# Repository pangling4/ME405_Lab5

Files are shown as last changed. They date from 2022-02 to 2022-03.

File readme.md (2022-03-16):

# ME 405 Winter 2022 Term Project: 3.5 Axis Machine
Created by Jonathan Cederquist, Tim Jain, and Philip Pang

## Introduction: Spider-Yoda, the 3-RRR Planar Parallel Robot
For this project our group designed, built, and tested a 3-RRR planar
parallel robot which we have nicknamed "Spider Yoda". This robot is
designed for us as a pen plotter for the average Joe who is interested
in a using a robotic companion to draw anything their heart desires.
Currently, it has only been used by the creators, but it could serve as
a device used to introduce high school or college students to robotics
and promote further interest and research in the field of robotics.

The overall functionality of the robot is quite simple. The moving
platform (which holds a Sharpie or other writing utensil) traces the
user's movements on the attached touchpad to produce a scaled drawing
of whatever path the user traces out. When the user places their finger
or stylus on the touchpad, the robot places the pen on the paper and
begins drawing whatever shape the user does. When the user lifts their
finger, the robot stops motion and the pen is retracted. In the future,
additional functionality may be added to allow the robot to draw on its
own from an uploaded image file. A schematic of a generic 3 RRR planar
parallel robot is shown below.

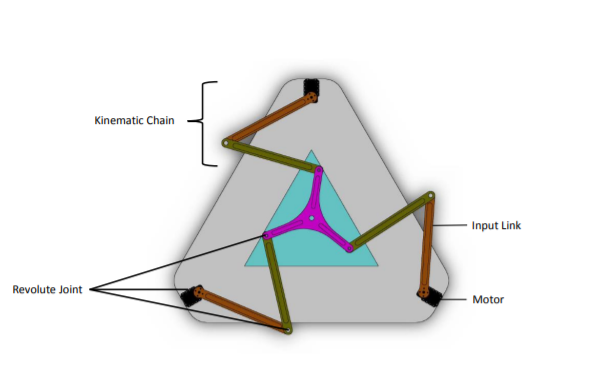
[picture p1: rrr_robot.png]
3-RRR Planar Parallel Robot!


*Figure 1: Schematic for a generic 3-RRR Planar Parallel Robot. [1]*

## Hardware Overview

### Bill of Materials
The following table shows the bill of materials used for our project. 
Minor components such as solder and wires are not included. It should
be noted that this table only lists the list price of each component,
tax and/or shippping are not included. This can be a significant
component of the project cost depending on the timeline and location
the products are sourced from.

| Qty. | Part | Source | Total Cost |
|:----:|:---|:---|:---: |
|  1 | Nucleo L476RG with Shoe | ME405 Tub | - |
|  6 | Aluminum Link | ME405 Scrap Bin | - |
|  1 | Aluminum Drawing Platform | ME405 Scrap Bin | - |
|  1 | 3D Printed Pen Holder | Friend's 3D printer | - |
|  1 | Black Fine Sharpie | Tim's Pencil Pouch | - |
|  ? | Other bolts/nuts | ME405 Hardware Stock  | - |
|  6 | M3-0.5 x 20mm SHCS | Home Depot | $1.98 |
|  1 | 2'x 2' Particle Board Base Plate | Home Depot | $4.23 |
|  15  | 1/4" Zinc Flat Washer | Home Depot | $2.40 |
|  10  | 1/4-20 Zinc Hex Nut | Home Depot | $1.28 |
|  3 | 6mm Set-Screw Shaft Collar 6056N14  | McMaster Carr | $5.31 |
|  6 | 5/16" Needle-Roller Thrust Bearing  | McMaster Carr | $19.14 |
|  6 | 5/16" Shoulder Screw | McMaster Carr | $8.52 |
|  3 | 12V Motor w/Encoder, 131 Gear Ratio | DFRobot | $87.00 |
|  1 | 12 VDC Open Frame Pull Solenoid | Chaocheng Technology  | $13.81 |
|  3 | MUZHI SPDT1NO Mtl Roller Lim Switch | Amazon | $1.83 |
|  3 | CHUANGRONG-US 1/3" SS Ball transfers| Amazon | $7.17 |

### Electronic Components
This project was built around the STM32 Nucleo L476RG microcontroller,
which was also equipped with the "Shoe of Brian" mounting board which
houses a USB on-the-go connector for easier file management. We also
used a DRI0039 quad motor driver shield from DFRobot, which implements
two TB6612FNG motor driver ICs, on top of the Nucleo to drive the three
gear motors and solenoid which lifted the pen. The motors used to drive
the motion of the links were FIT0185 DFRobot gear motors with encoders,
which have a 131:1 gear ratio and 2096 encoder counts per revolution on
the output shaft. The only other major electronic components were the
three roller limit switches, which were used in the calibration of the
robot before drawing began.

### Mechanical Components
Most of the structural mechanical components were found from the ME 405
scrap bin or purchased from Home Depot. The motors served as the stand
for the base platform, which was a 5/8"x2'x2' sheet of particle board
with holes drilled out for the motor shafts. The links and drawing
platform were aluminum scrap with holes reamed in them for close
fitting to the shoulder bolts. Each revolute joint connection included
two washers, a needle-roller thrust bearing to reduce friction, and a
shoulder bolt with a hex nut. The drawing platform itself had the 3D
printed pen holder and solenoid attached, along with ball transfers on
the bottom to support the platform and reduce friction as the robot
moved along the base plate. The rest of the components included wires,
attachement materials (hot glue, tape), and 3D printed limit switch
mounts which allowed the a-links to hold the limit switches for
calibration.

## Software Overview
This section summarizes the software organization for this project with
a task diagram and state transition diagram. The detailed documentation
is found on the doxygen mainpage, linked below:
https://pangling4.github.io/TermProject/

### Task Diagram
This section briefly explains the task organization for the cooperative
multitasking used in this project. The five tasks that were run by the
priority scheduler are shown below in the task diagram. Each joint task
consists of a RoboMotorDriver, a RoboEncoderDriver, and a ClosedLoop 
controller. The joint tasks receive the desired angle from the brain
and perform closed loop PI control using the motor and encoder to move
the link to the desired position. The angles are computed in the brain
from the inverse kinematic equations and the x and y coordinate which
are read from the touchpad.The readyFlag allows the motors and solenoid
to be shut off when the robot is ready to be shut down.

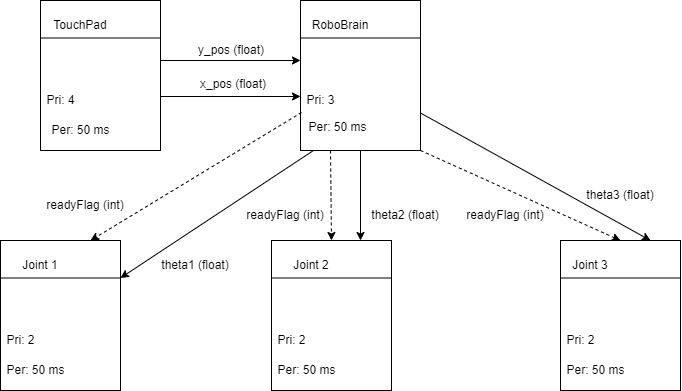
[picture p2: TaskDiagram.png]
3DOF Parallel Robot Task Diagram!


*Figure 2: Task Diagram for 3-RRR Planar Parallel Robot.*

### State Transition Diagram
The state transition diagram for our robot is shown below. The simple
layout is explained in more detail on the doxygen mainpage.

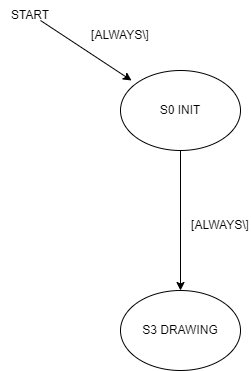
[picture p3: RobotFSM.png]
3DOF Parallel Robot State Transition Diagram!


*Figure 3: State Transition Diagram for 3-RRR Planar Parallel Robot.*

## Results
Overall, due to the limited timeline for the project, the system has
not been extensively tested. During the development of the controller
for the system, the motors underwent step response tests to determine
appropriate proportional and integral gains. However, these tests were
performed without any load on the motor shaft, as attaching the links
during a step response could damage the robot.

After final assembly, the robot was tested by having users draw on the
touchpad and observing the behavior. The robot's intended functionality
was evident in these tests, although it did not perform to our
satisfaction. One of the major problems we found was that the nature of
a parallel robot having interconnected and interdepedent links often
caused the robot to 'lock up' in a degenerate position where it could 
not move any of its links. When this happened, we had to restart the
robot and manually move the links back to a position where they could
move freely.

Other issues we became aware of during testing were the backlash in the
a-links and the method of control for the inverse kinematics. Both of 
these issues contributed to 'sloppy' behavior for the drawing platform,
since a motion on the touchpad would either not be large enough to 
cause a motion on the platform (due to small angle changes and large 
backlash), or the motion would be overwritten by the next motion since
the links were not able to respond fast enough. Thus, the actual motion
of the drawing platform did not match the motion of the user's hand on
the touchpad.

## Project Learning Outcomes
Overall, this project was more difficult and time-consuming than we
expected, mainly because of the mechanical complexities in our design
and difficulties we encountered during manufacturing and assembly. The
following sections describe some of the major difficulties we faced and
future recommendations for others who build a similar robot.

### Difficulties Encountered
One major problem we encountered while assembling our robot was getting
the a-links to attach securely to the motor shafts. Our original design 
used steel shaft collars with set screws that would be epoxied to the
a-links and then securely tightened onto the d-flat of the motor shaft.
However, the shaft collars would consistently fall off of the a-links
during testing and loading, likely because the surfaces were not well
prepared for epoxy and possibly because the metals being bonded were
not the same (steel vs aluminum). In the final robot, we used d-shaped
holes waterjet into the links directly, but due to the small difference
in diameter between the motor shaft OD and d flat, these ended up
having large amounts of backlash.

Another issue we encountered was in calibration. After creating the 3D
printed mounts for the limit switches and ramps used to locate a known
location for each link, we realized that having the mounts on the links
interfered with the robot motion in some configurations. This could 
have been mitigated by shifting the limit switches closer to the motors
on the link; however, the ramp had already been glued down on the base.
One solution to this problem would be to make longer ramps to allow the
limit switch to slide along the link to any necessary location. An even
better solution would be to embedd the limit switches in the base and
mount the ramps to the bottom of the link, thus reducing the wiring
complexity and allowing the links to move freely without interference.
However, due to the time constraint on the project, we were not able to
implement these improvements.

### Future Recommendations
Overall, the most important recommendation we can offer anyone desiring
to build a similar project is to spend adequate time on the mechanical
design. Creating detailed models, testing the connection methods and
layout, and iterating on failed designs are all important steps in the
design process that should not be skipped. Even the best-written
software is useless if the motor shaft is not securely attached to the
robot link.

Part of the challenge on this project for our team was the limited time
given to complete it. Do not underestimate the time necessary for 
manufacturing your robot. In addition, it is very helpful to buy or
make spare parts for your robot, since you never know when your epoxy connection will 
shear off and you will need to take 45 minutes to use a tiny 1/2" thick hacksaw
blade to gnaw away a stripped shoulder bolt at 1 am the night before it is due.
Other complications could be that a screw head
will strip, or glue will come loose, or other issue will occur that requires a
replacement. Software can be updated and improved (relatively) easily,
requiring only time to debug and test. On the other hand, updating or
improving mechanical hardware can be significantly more challenging,
especially if tools or materials are not readily available.

## CAD
The mechanical design for this project was performed in SolidWorks. All
of the models created for the project can be found under the src folder
in the CAD Rev4 folder, which has been updated to reflect the actual
dimensions and layout of the robot as-built. The wiring and attachment
components (such as tape and hot glue) are not shown.

Link: https://github.com/pangling4/TermProject/tree/main/src/CAD%20Rev4

[1] G. Johnston, R. Yasin, L. Wang, N. Sarli, and N. Simaan, “Parallel 
3RRR Robot Classroom Guide,” 07-Jul-2016. [Online]. Available: 
http://nri-csa.vuse.vanderbilt.edu/joomla/images/Harpeth_Hall_Winterim/Parallel_3RRR_Robot_Classroom_Guide.pdf. [Accessed: 25-Feb-2022].

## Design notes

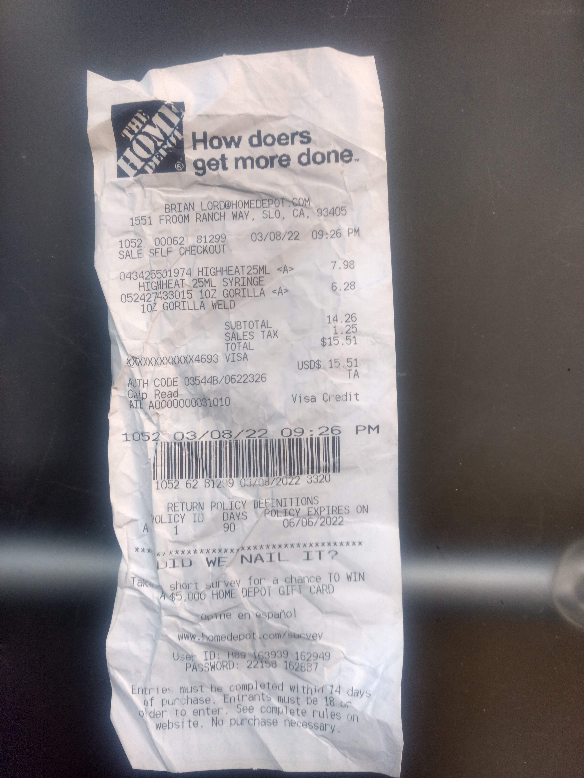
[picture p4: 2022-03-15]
Epoxy1.jpg

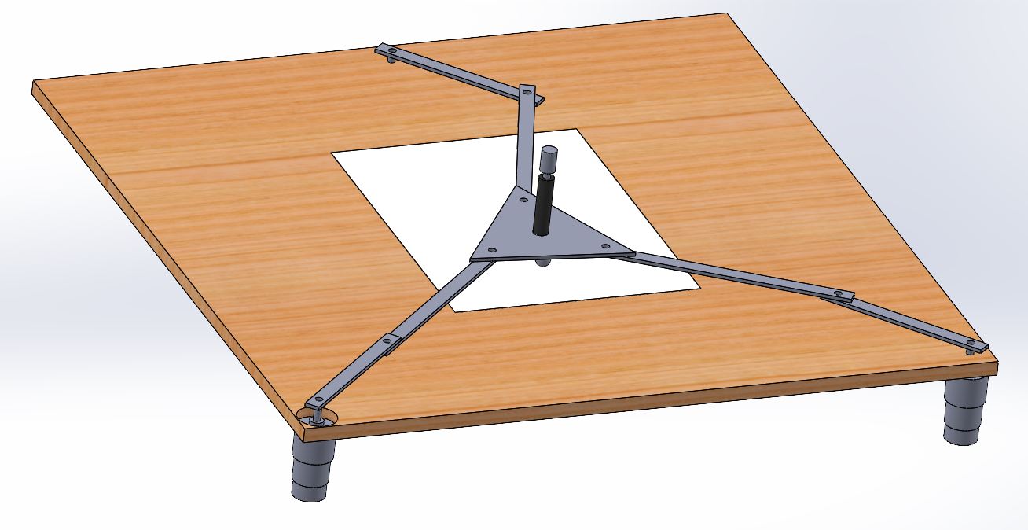
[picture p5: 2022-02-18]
3R_iso_2.JPG

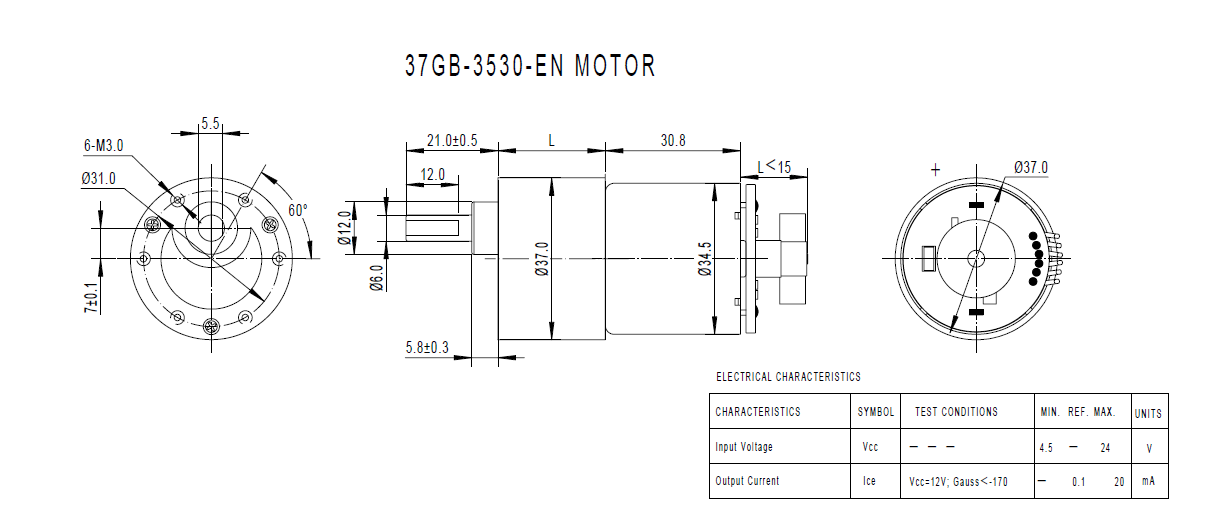
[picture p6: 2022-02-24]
motor_dims.png

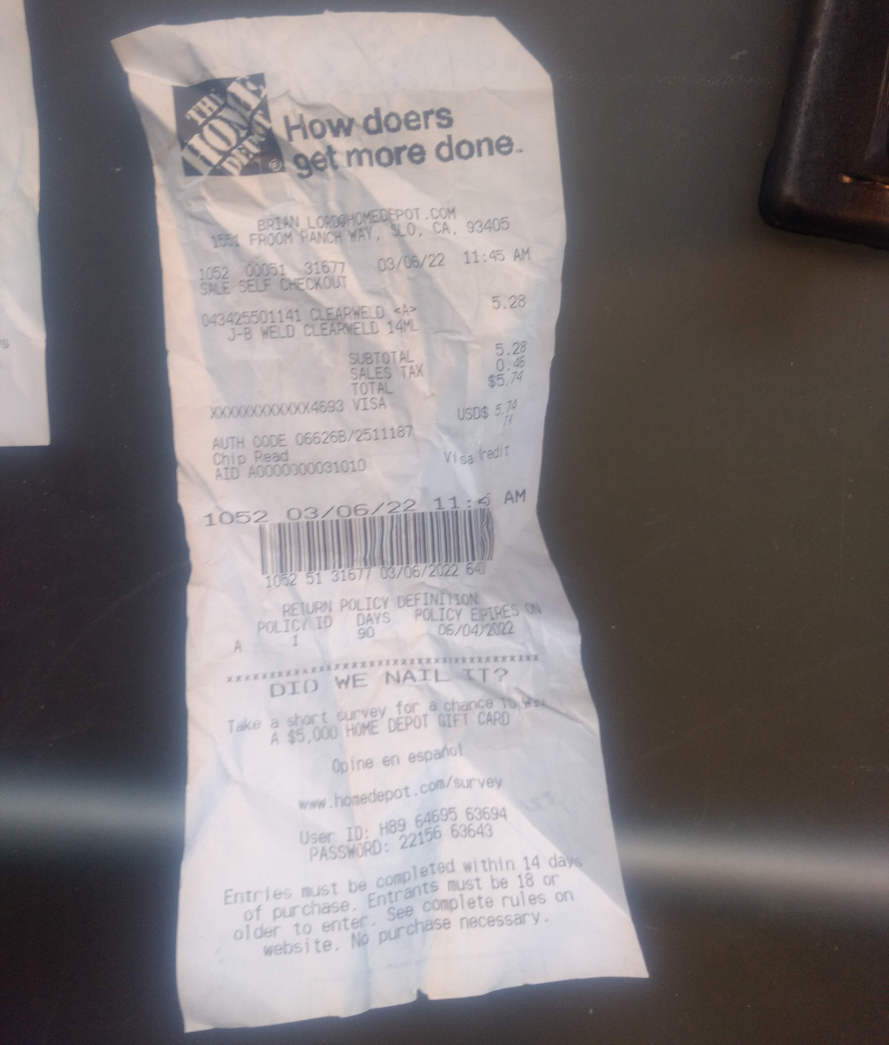
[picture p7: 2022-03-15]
JBWeld.jpg

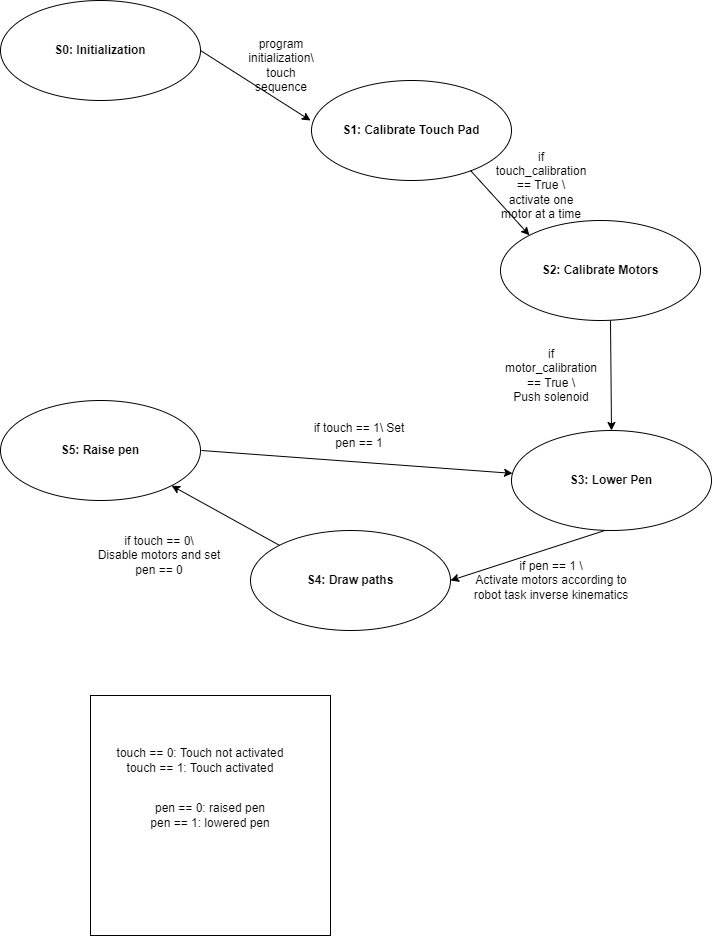
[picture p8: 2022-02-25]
3R_FSM_Touch.drawio.png

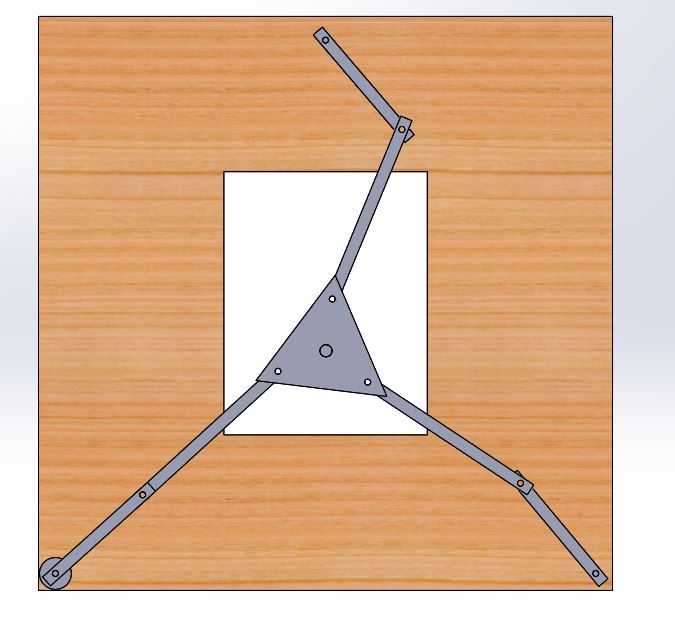
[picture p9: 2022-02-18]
3R_top_cad.JPG

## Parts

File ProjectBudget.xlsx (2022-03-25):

Item | Quantity | Per Item | Price | Buyer | Vendor
JB ClearWeld | 1 | $5.74 | $5.74 | Tim | Home Depot
HighHeat Epoxy | 1 | $7.98 | $7.98 | Tim | Home Depot
Thrust Bearings | 6 | $3.19 | $19.14 | Tim | McMaster-Carr
Shoulder Screws | 6 | $1.42 | $8.52 | Tim | McMaster-Carr
Shaft Collar | 3 | $1.77 | $5.31 | Tim | McMaster-Carr
Unthreaded Spacers | 3 | $1.77 | $5.31 | Tim | McMaster-Carr
McMaster Shipping and Tax | 1 | $11.88 | $11.88 | Tim | McMaster-Carr
 |  |  | $0.00
 |  |  | $0.00
 |  |  | $0.00
 |  |  | $0.00
 |  |  | $0.00
 |  |  | $0.00
 |  |  | $0.00
 |  |  | $0.00
 |  |  | $0.00
 |  |  | $0.00
 |  |  | $0.00
 |  |  | $0.00

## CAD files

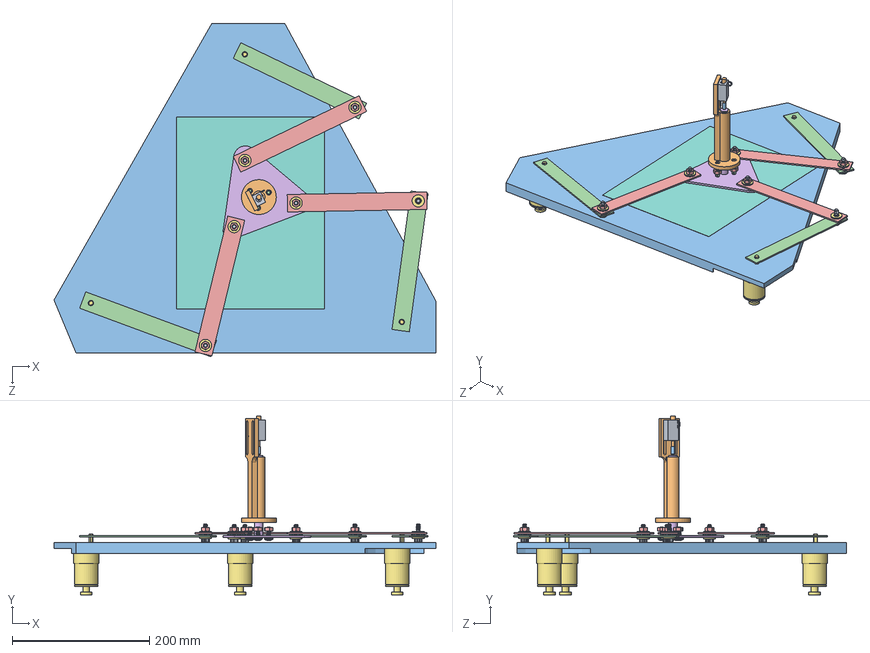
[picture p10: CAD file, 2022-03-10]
src/CAD Rev4/10_Full_3R_Assembly_rev4.SLDASM
555.8 x 260.0 x 485.0 mm
01_Base_Plate_rev4
02_A_Link x 3
03_B_Link x 3
05_Pen
07_Motor_rev2 x 3
5909K24_Needle-Roller Thrust Bearing x 6
91259A576_Alloy Steel Shoulder Screw x 6
PenHolder
Solenoid_Mount
Solenoid_Shaft
Solenoid_Cap
90604A539_Pan Head Combination Phillips Slotted Screws x 3
95462A029_Medium-Strength Steel Hex Nut x 9
Platform_Alt
90850A150_Grade 9 Steel Washer x 12
06_Paper

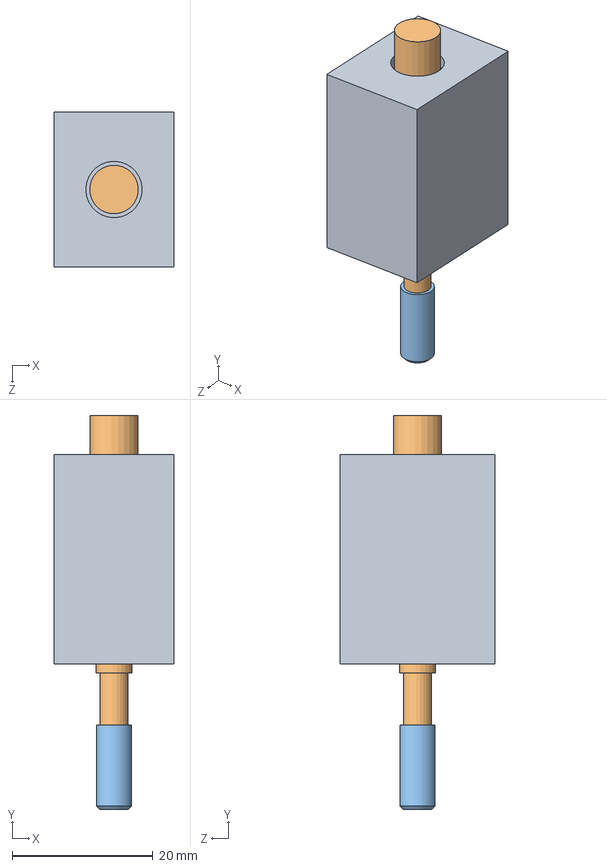
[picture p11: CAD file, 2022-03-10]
src/CAD Rev4/SolenoidAssembly.SLDASM
17.0 x 55.9 x 22.0 mm
Solenoid_Mount
Solenoid_Shaft
Solenoid_Cap

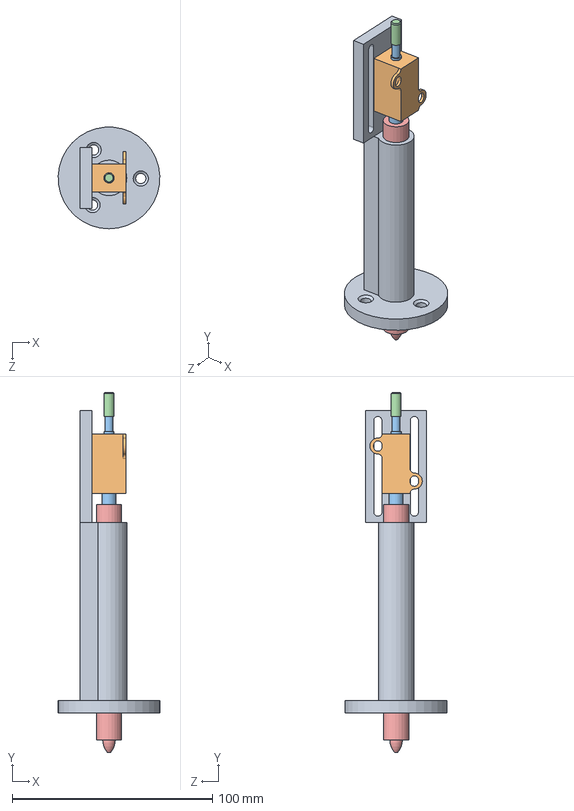
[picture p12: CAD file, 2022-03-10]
src/CAD Rev4/PenHoldingAssembly.SLDASM
50.7 x 179.7 x 50.7 mm
PenHolder
Solenoid_Mount
Solenoid_Shaft
Solenoid_Cap
05_Pen

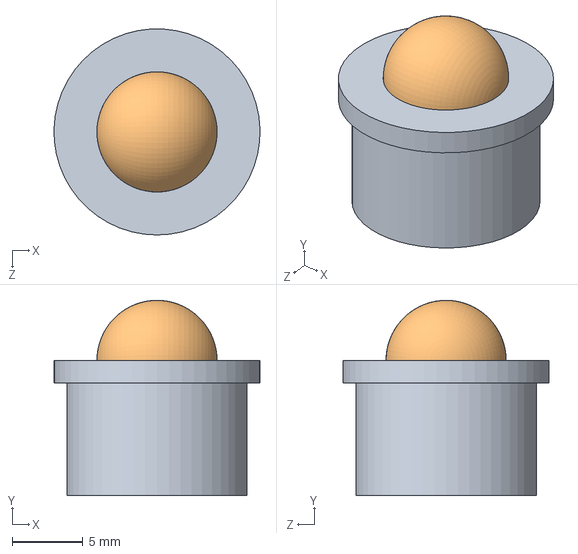
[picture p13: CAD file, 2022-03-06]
src/CAD Rev4/10_Ball_Transfer.SLDASM
14.5 x 13.8 x 14.5 mm
09_Ball_Holder
08_Ball

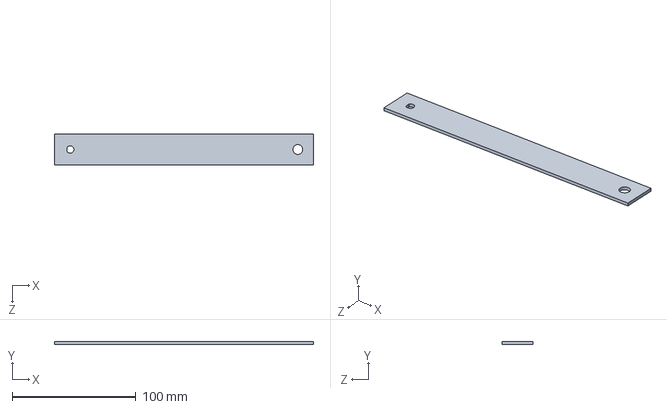
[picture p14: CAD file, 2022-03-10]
src/CAD Rev4/Master_Link.SLDPRT
209.5 x 2.29 x 25.4 mm

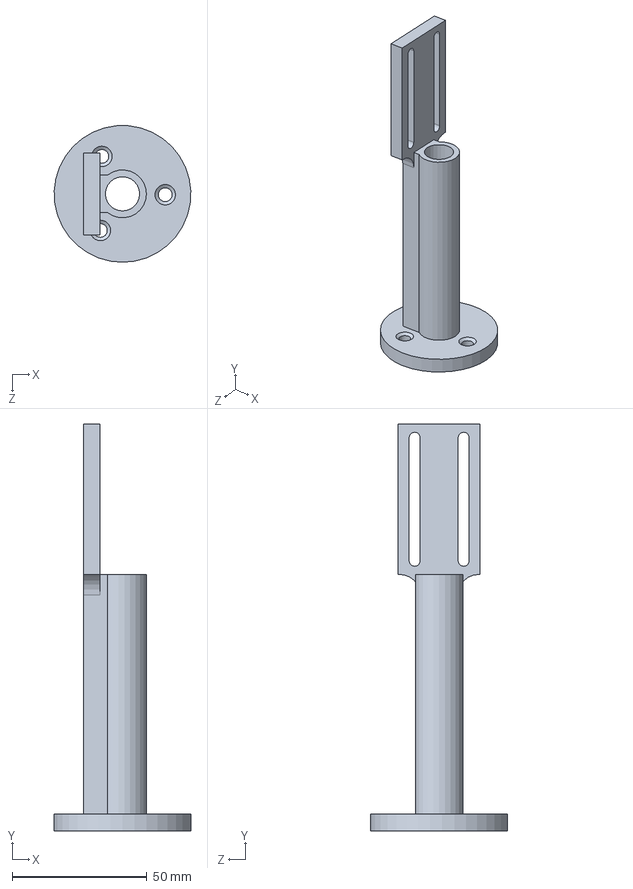
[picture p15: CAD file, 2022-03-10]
src/CAD Rev4/PenHolder.SLDPRT
50.7 x 151.1 x 50.7 mm

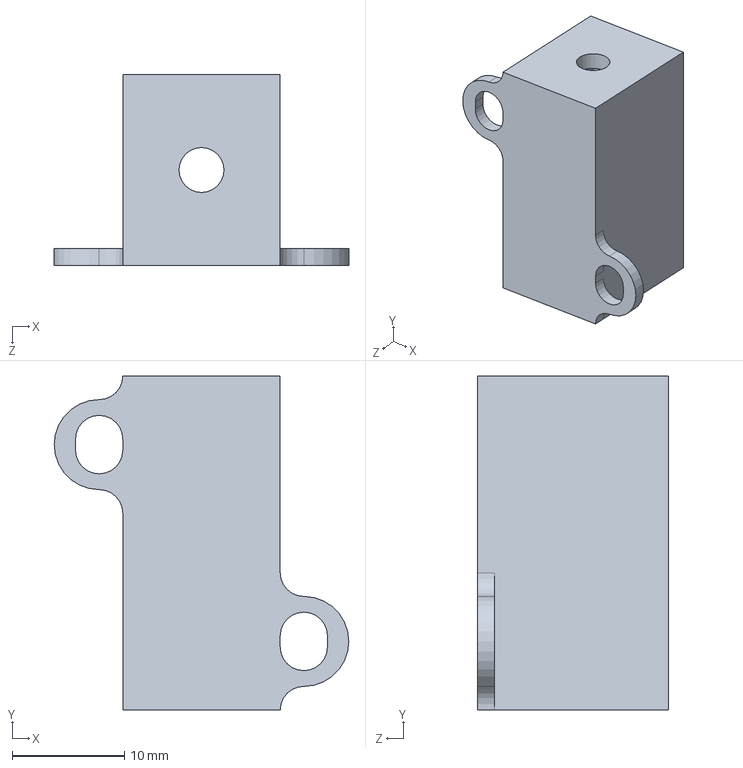
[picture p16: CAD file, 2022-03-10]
src/CAD Rev4/Solenoid_Mount.SLDPRT
26.2 x 29.7 x 17.0 mm

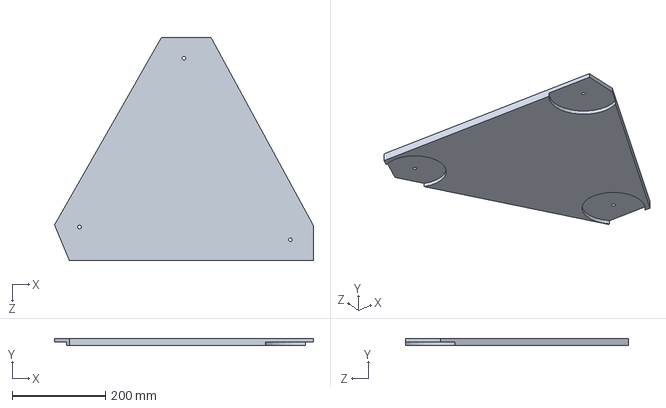
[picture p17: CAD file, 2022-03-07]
src/CAD Rev4/01_Base_Plate_rev4.SLDPRT
555.8 x 15.9 x 479.4 mm

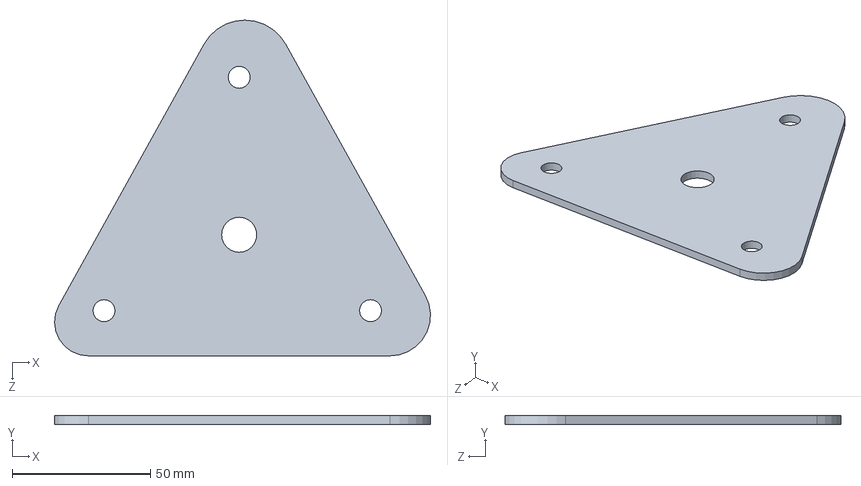
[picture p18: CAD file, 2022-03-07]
src/CAD Rev4/Platform_Alt.SLDPRT
136.0 x 3.17 x 121.5 mm

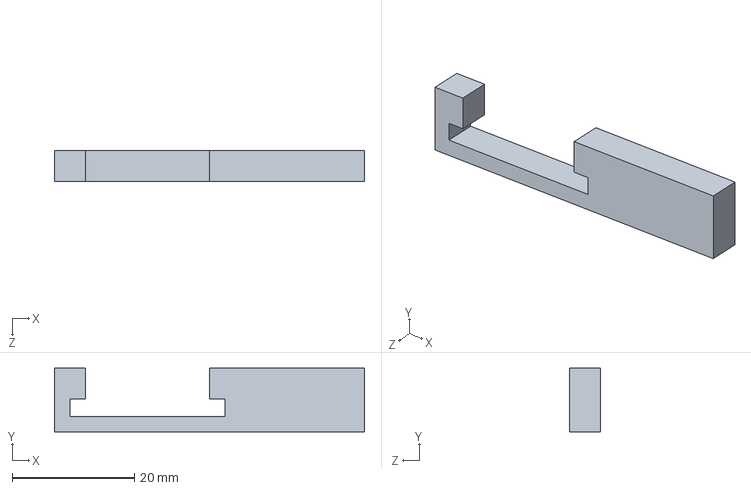
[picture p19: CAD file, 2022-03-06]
src/CAD Rev4/12_Limit_Mount.SLDPRT
50.8 x 10.4 x 5.08 mm

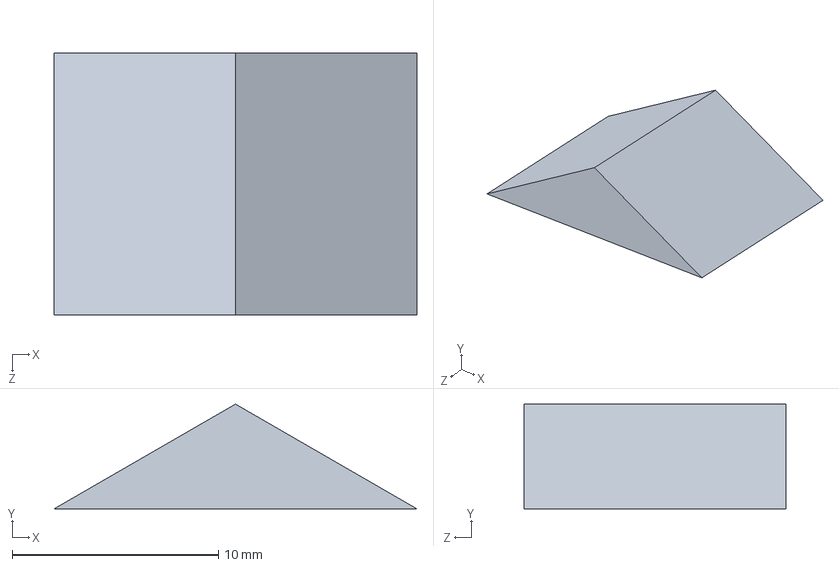
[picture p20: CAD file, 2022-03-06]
src/CAD Rev4/13_Limit_Ramp.SLDPRT
17.6 x 5.08 x 12.7 mm

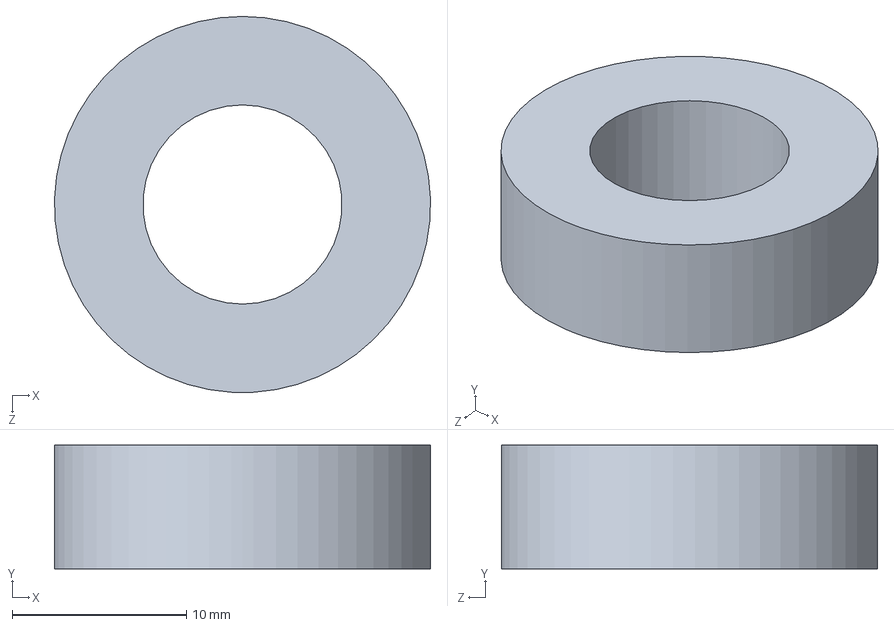
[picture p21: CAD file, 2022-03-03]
src/CAD Rev4/09_Ball_Holder.SLDPRT
21.6 x 7.11 x 21.6 mm

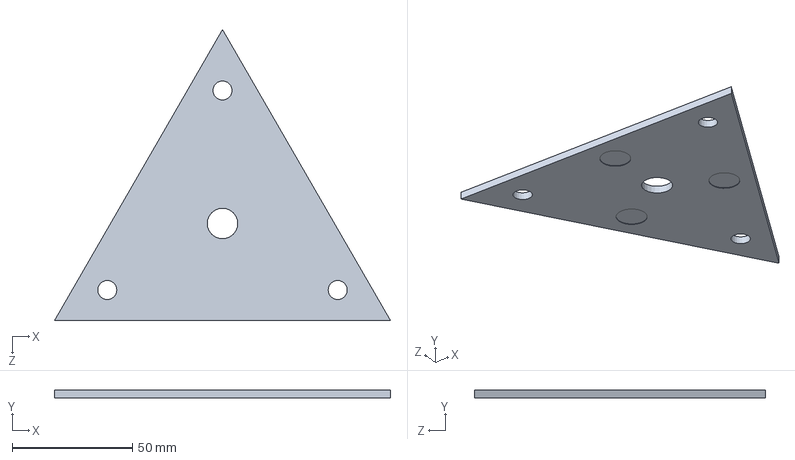
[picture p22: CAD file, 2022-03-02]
src/CAD Rev4/04_Platform.SLDPRT
140.0 x 3.17 x 121.2 mm

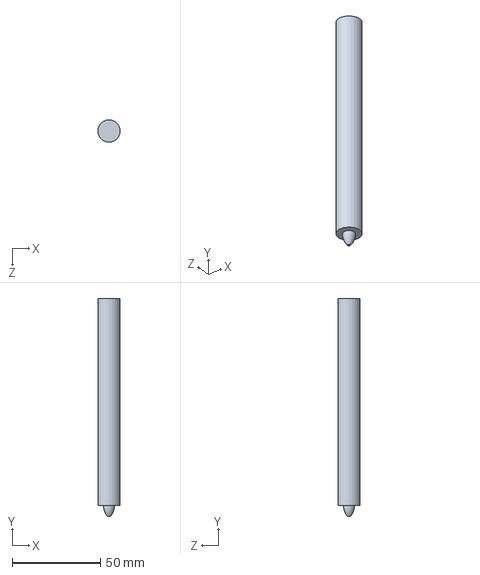
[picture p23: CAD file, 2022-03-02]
src/CAD Rev4/05_Pen.SLDPRT
12.7 x 123.8 x 12.7 mm

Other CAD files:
src/CAD Rev4/Solenoid_Cap.SLDPRT
src/CAD Rev4/Solenoid_Shaft.SLDPRT
src/CAD Rev4/07_Motor_rev2.SLDPRT
src/CAD Rev4/grainger-2alx5.sldprt
src/CAD Rev2/01_Base_Plate.SLDPRT
src/CAD Rev2/01_Base_Plate_rev2.SLDPRT
src/CAD Rev2/01_Base_Plate_rev3.SLDPRT
src/CAD Rev2/02_A_Link.SLDPRT
src/CAD Rev2/03_B_Link.SLDPRT
src/CAD Rev2/06_Paper.SLDPRT
src/CAD Rev2/10_Full_3R_Assembly_rev2.SLDASM
src/CAD Rev2/10_Full_3R_Assembly_rev3.SLDASM
src/CAD Rev2/11_Solenoid_rev2.SLDPRT
src/CAD Rev2/1_ALink.SLDPRT
src/CAD Rev2/Motor_Mount.SLDPRT
src/CAD Rev2/Spacer_Platform.SLDPRT
src/CAD Rev4/02_A_Link.SLDPRT
src/CAD Rev4/03_B_Link.SLDPRT
src/CAD Rev4/08_Ball.SLDPRT
src/CAD Rev4/08_Roller.SLDPRT
src/CAD Rev4/5909K24_Needle-Roller Thrust Bearing.SLDPRT
src/CAD Rev4/6056N14_Carbon Steel Set Screw Collar.SLDPRT
src/CAD Rev4/90604A539_Pan Head Combination Phillips Slotted Screws.SLDPRT
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

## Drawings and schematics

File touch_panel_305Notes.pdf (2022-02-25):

# Lecture 21 - 4-Wire Resistive Touch Panels

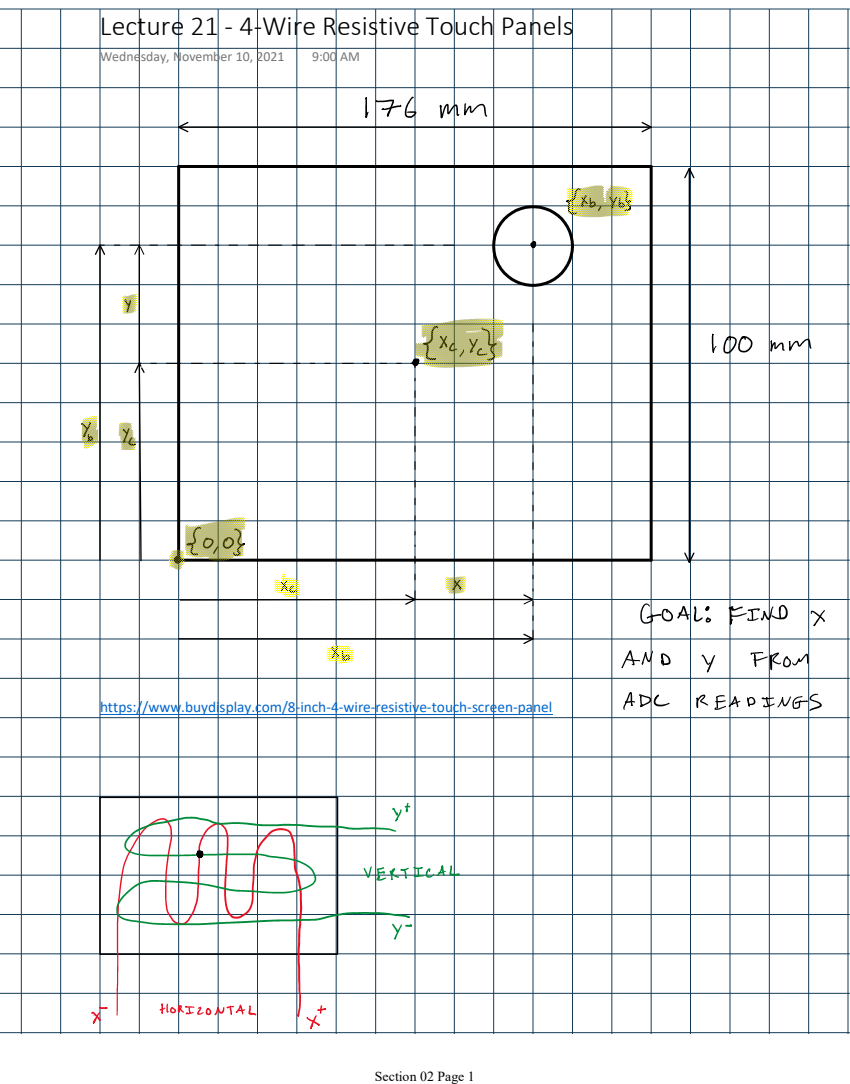
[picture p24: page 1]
Wednesday, November 10, 2021; Section 02 Page 1

https://www.buydisplay.com/8-inch-4-wire-resistive-touch-screen-panel

# Equivalent Circuit

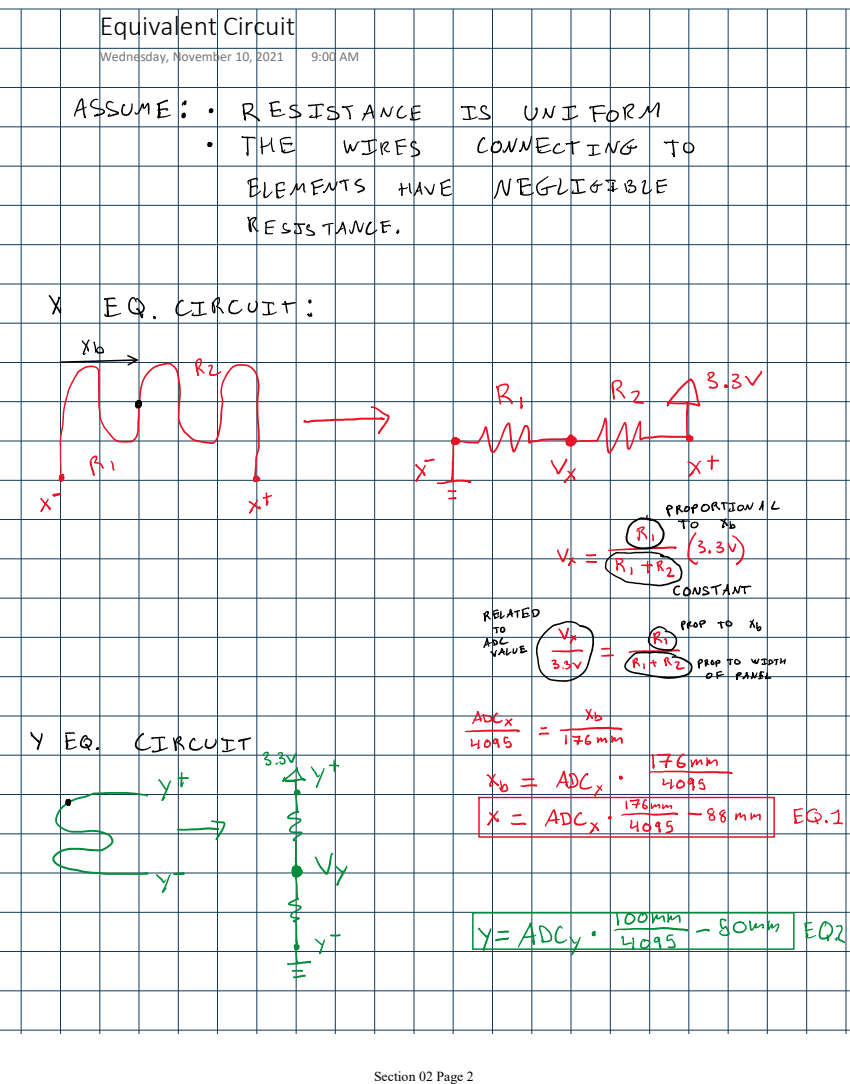
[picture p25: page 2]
Section 02 Page 2

# X Scan

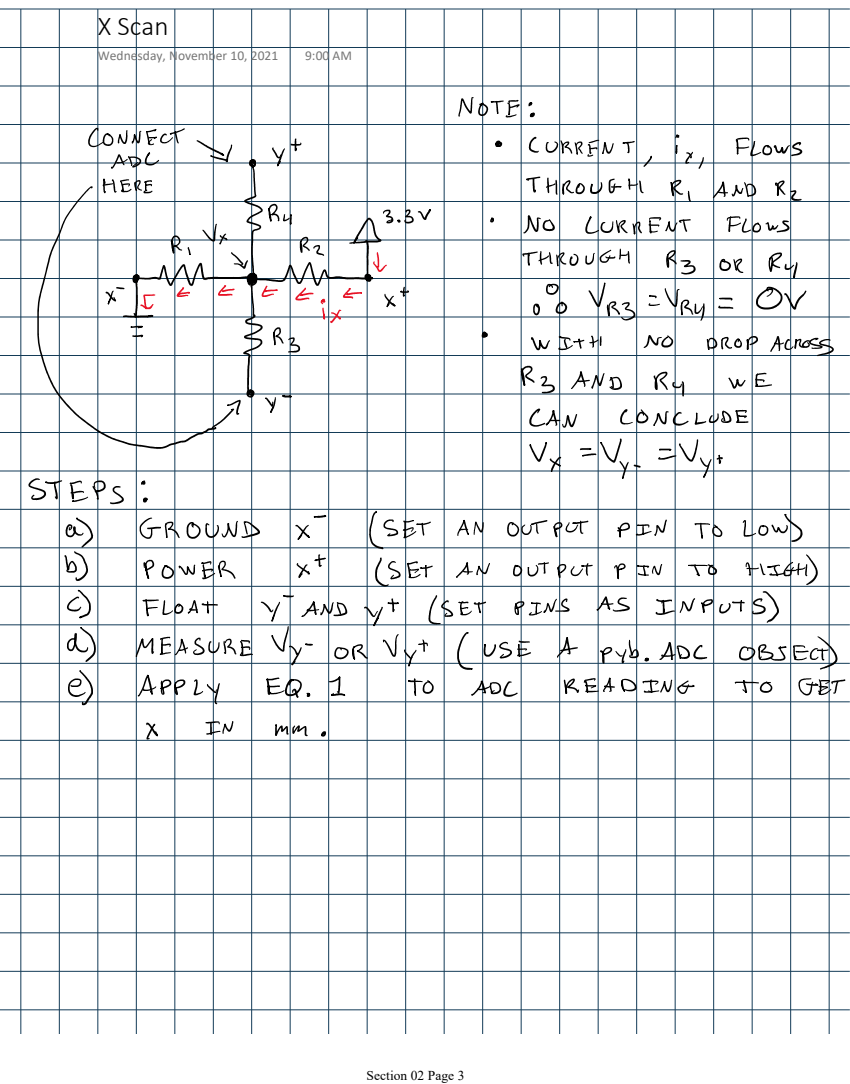
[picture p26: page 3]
Section 02 Page 3

# Y Scan

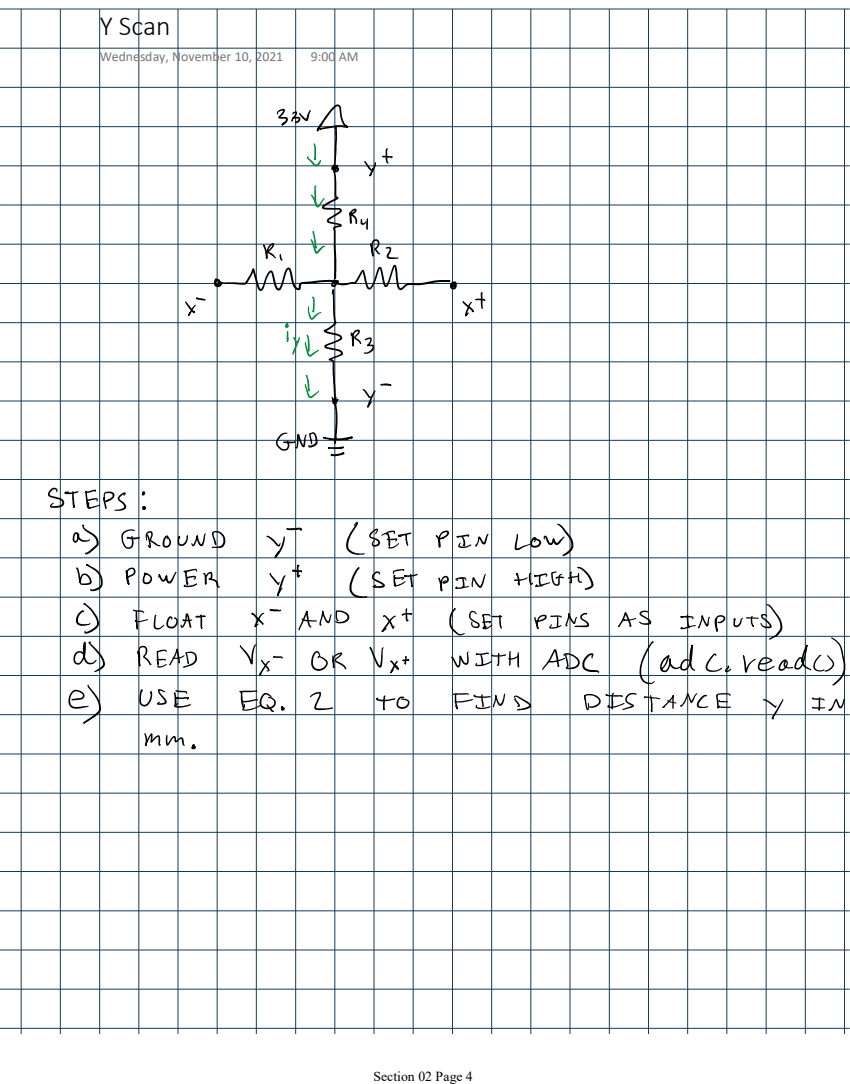
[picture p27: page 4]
Section 02 Page 4

# Z Scan

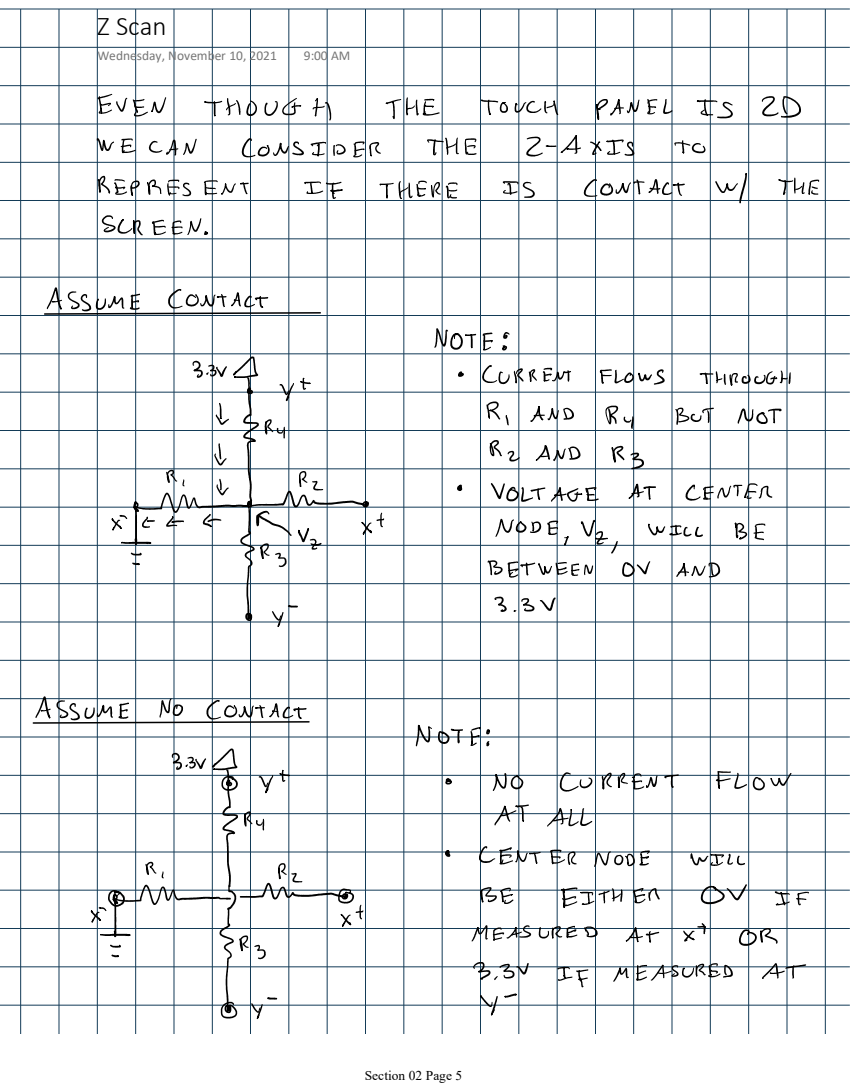
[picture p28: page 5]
Section 02 Page 5

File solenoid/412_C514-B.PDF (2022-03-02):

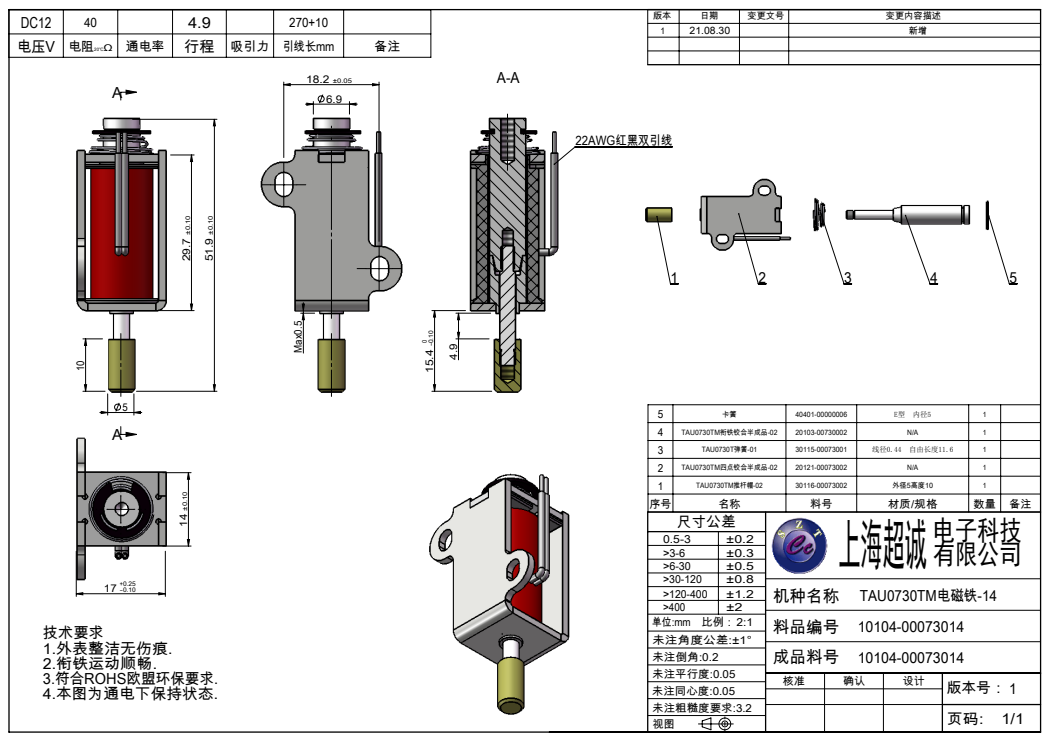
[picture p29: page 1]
2:1 技术要求

5 | 卡簧 | 40401-00000006 | E型 内径5 | 1
4 | TAU0730TM衔铁铰合半成品-02 | 20103-00730002 | N/A | 1
3 | TAU0730T弹簧-01 | 30115-00073001 | 线径0.44 自由长度11.6 | 1
2 | TAU0730TM四点铰合半成品-02 | 20121-00073002 | N/A | 1
1 | TAU0730TM推杆帽-02 | 30116-00073002 | 外径5高度10 | 1
序号 | 名称 | 料号 | 材质/规格 | 数量 | 备注
尺寸公差 | 上海超诚 电子科技 有限公司
0.5-3 | ±0.2
>3-6 | ±0.3
>6-30 | ±0.5
>30-120 | ±0.8

核准 | 确认 | 设计 版本号： 1 1/1 页码:

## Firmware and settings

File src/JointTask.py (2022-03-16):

'''!
@file       jointTask.py
@brief      Implements motor, encoder, and controller to control joints
@details    Creates a motor driver, encoder, and closed loop controller corresponding to
            a joint on the 3RRR planar parallel robot. The run function is used by
            the cotask scheduler to control the motion of each joint
@author     Jonathan Cederquist
@author     Tim Jain
@author     Philip Pang
@date       Last Modified 3/5/22
'''

import pyb
import utime
import RoboMotorDriver
import RoboEncoderDriver
import ClosedLoop

class JointTask:
    '''! 
    This class implements a motor, encoder, and control task to control robot joints. 
    '''
    
    def __init__ (self, ready, motor_const, encoder_const, kp, ki, setpoint, queue_theta):
        '''! 
        @brief                  Creates a JointTask object
        @details                Creates RoboMotorDriver, RoboEncoderDriver, and ClosedLoop
                                controller objects corresponding to the given constants to
                                control the motion of a joint on the 3 RRR planar parallel
                                robot.
        @param ready            A task_share.Share variable that is used as a flag to turn
                                off the joint motor when the robot shuts down
        @param motor_const      An integer denoting the motor associated with the joint.
                                Motor 1 corresponds to M1, pins PB5 and PB3
                                Motor 2 corresponds to M2, pins PA6 and PA7
                                Motor 3 corresponds to M3, pins PA9 and PB4
        @param encoder_const    An integer denoting the encoder associated with the motor.
                                Encoder 1 corresponds to pins PB6 and PB7 with timer 4
                                Encoder 2 corresponds to pins PC6 and PC7 with timer 8
                                Encoder 3 corresponds to pins PA0 and PA1 with timer 5
        @param kp               The proportional gain constant used for the closed loop controller
                                The constant should be given in units of [% duty cycle/degree]
        @param ki               The integral gain constatn used for the closed loop controller
                                The constant should be given in units of [% duty cycle * sec/degree]
        @param setpoint         The setpoint in degrees for the closed loop controller
        @param queue_theta      The task_share.Queue corresponding to this joint's theta value
        '''
        
        self.motor_const = motor_const
        
        self.ready = ready
        
        # Check motor number and create corresponding RoboMotorDriver
        if motor_const==1:
            pinB5 = pyb.Pin(pyb.Pin.board.PB5, pyb.Pin.OUT_PP)
            pinB3 = pyb.Pin(pyb.Pin.board.PB3, pyb.Pin.OUT_PP)
    
            self.motor = RoboMotorDriver.RoboMotorDriver(pinB5, pinB3, 2, 2)
            
        elif motor_const==2:
            pinA6 = pyb.Pin(pyb.Pin.board.PA6, pyb.Pin.OUT_PP)
            pinA7 = pyb.Pin(pyb.Pin.board.PA7, pyb.Pin.OUT_PP)
    
            self.motor = RoboMotorDriver.RoboMotorDriver(pinA6, pinA7, 3, 2)
            
        elif motor_const==3:
            pinA9 = pyb.Pin(pyb.Pin.board.PA9, pyb.Pin.OUT_PP)
            pinB4 = pyb.Pin(pyb.Pin.board.PB4, pyb.Pin.OUT_PP)
    
            self.motor = RoboMotorDriver.RoboMotorDriver(pinA9, pinB4, 3, 1)
        
        self.motor.set_duty_cycle(0)
        
        # Check encoder number and create corresponding RoboEncoderDriver
        if encoder_const==1:
            self.encoder = RoboEncoderDriver.RoboEncoderDriver(pyb.Pin(pyb.Pin.board.PB6), pyb.Pin(pyb.Pin.board.PB7), 4)
            
        elif encoder_const==2:
            self.encoder = RoboEncoderDriver.RoboEncoderDriver(pyb.Pin(pyb.Pin.board.PC6), pyb.Pin(pyb.Pin.board.PC7), 8)
            
        elif encoder_const==3:
            self.encoder = RoboEncoderDriver.RoboEncoderDriver(pyb.Pin(pyb.Pin.board.PA0), pyb.Pin(pyb.Pin.board.PA1), 5)
            
        # Create closed loop controller
        self.controller = ClosedLoop.ClosedLoop(kp, ki, setpoint)
        
        # Create variable to access queue of position values
        self.theta_queue = queue_theta
        
        # Create joint angle value
        self.theta = 0
        
        # Run calibration on creation of each joint
        self.calibrate()
        
        
    def run(self):
        '''!
        @brief      Generator which continuously updates the joint
        @details    Pulls the desired position from a shared queue, and updates
                    the joint motor, encoder, and controller accordingly
        '''
        
        while True:
            #Update angle from shared kinematics
            
            if self.ready.get() == 0:
                self.motor.set_duty_cycle(0)
                print("Motor Off")
                
            else:
                if self.theta_queue.any():
                    newTheta = self.theta_queue.get()
                else:
                    newTheta = self.theta
                if self.theta != newTheta:
                    self.theta = newTheta
                    self.controller.change_setpoint(self.theta)
                
                # Update encoder and change control signal
                self.encoder.update()
                self.motor.set_duty_cycle(self.controller.update(self.encoder.read()))
            yield(0)

    def calibrate(self):
        '''!
        @brief      Calibrates the joint encoder to the correct position
        @details    Waits for the user to manually move the link past the limit
                    switch ramp and sets the encoder value to the correct angle
                    after the link has moved back and forth across the limit
                    switch ramp.
        '''
        
        if self.motor_const == 1:
            limit = pyb.Pin(pyb.Pin.cpu.C4, pyb.Pin.PULL_DOWN)
            theta1 = 4
            theta2 = 6
        elif self.motor_const == 2:
            limit = pyb.Pin(pyb.Pin.cpu.C1, pyb.Pin.PULL_DOWN)
            theta1 = 122
            theta2 = 124
        elif self.motor_const == 3:
            limit = pyb.Pin(pyb.Pin.cpu.A5, pyb.Pin.PULL_DOWN)
            theta1 = 242
            theta2 = 243
        
        print("Calibrating motor " + str(self.motor_const))
        
        count = 0
        press = 0
        clicks = [0, 0]
        
        while True:
            self.encoder.update()
            if press == 1 and limit.value() == 0:
                press = 0
            if press == 0 and limit.value() == 1:
                clicks[count] = self.encoder.read()
                count += 1
                press = 1
                print("Limit found")
                
                if count == 2:
                    if(clicks[0] > clicks[1]):
                        self.encoder.setTheta(theta1)
                    elif (clicks[1] > clicks[0]):
                        self.encoder.setTheta(theta2)
                    else:
                        self.encoder.setTheta((theta1+theta2)/2)
                    print("calibration complete")
                    break
                
        
if __name__ == "__main__":
    pass
    

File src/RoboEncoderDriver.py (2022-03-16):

'''!
@file       roboEncoderDriver.py
@brief      Used to read from encoders attached to motors (No. GB37Y3530-12V-83R)
@details    Utilizes alternate functions from timer channels on pyb board to 
            read from attached encoders
@author     Jonathan Cederquist
@author     Tim Jain
@author     Philip Pang
@date       Last Modified 3/3/22
'''

import pyb
import utime
import RoboMotorDriver

class RoboEncoderDriver:
    '''! 
    This class implements an encoder driver for an ME 405 Robot. 
    '''
    gearRatio = 131
    CPR = 16
    
    def __init__ (self, in1pin, in2pin, timer):
        '''! 
        @brief          Creates an RoboEncoderDriver object
        @details        Creates a RoboEncoderDriver by initializing timers and channels with 
                        given pins and timer number
        @param in1pin   A pyb.Pin object corresponding to the encoder channel A 
        @param in2pin   A pyb.Pin object corresponding to the encoder channel B
        @param timer    The timer number corresponding to the encoder pins
        '''
        
        # Create timer and timer channels in encoder mode
        self.timer = pyb.Timer(timer, prescaler = 0, period = 65535)
        self.ch1 = self.timer.channel(1, pyb.Timer.ENC_A, pin = in1pin)
        self.ch2 = self.timer.channel(2, pyb.Timer.ENC_B, pin = in2pin)
        
        # Stores current encoder position in radians
        self.current_position = 0
        self.delta = 0
        

    def update(self):
        '''!
        @brief      Updates the position of the encoder 
        @details    Updates the position of the encoder using saved last value
                    Checks for a 'valid' delta and adjusts if needed, then adds
                    delta to previous position 
        '''

        prev_position = self.current_position % 65535
        self.delta = self.timer.counter() - prev_position
        
        # Validate and adjust delta
        if self.delta < -65535/2:
            self.delta += 65535
        elif self.delta > 65535/2:
            self.delta -= 65535
        
        # Update position
        self.current_position += self.delta
        return self.current_position
    
    def read (self):
        '''!
        @brief      Returns current position of encoder
        @details    Converts the current encoder position reading (in ticks)
                    to degrees using the encoder CPR and gear ratio
        '''        
        return self.current_position * 180 / (self.gearRatio*self.CPR)
    

    def zero(self):
        '''!
        @brief      Zeros the encoder position
        '''
        
        self.current_position = 0
        self.delta = 0
        self.timer.counter(0)
    
    def setTheta(self, theta):
        '''!
        @brief       Sets the theta position of the encoder to the given value
        @param theta The angle (in degrees) to set the encoder's position to
        '''
        self.current_position = theta*self.gearRatio*self.CPR/180
        self.delta = 0
        self.timer.counter(0)
        
        
if __name__ == "__main__":
    
    encoder1 = RoboEncoderDriver(pyb.Pin(pyb.Pin.board.PB6), pyb.Pin(pyb.Pin.board.PB7), 4)
    encoder2 = RoboEncoderDriver(pyb.Pin(pyb.Pin.board.PC6), pyb.Pin(pyb.Pin.board.PC7), 8)
    encoder3 = RoboEncoderDriver(pyb.Pin(pyb.Pin.board.PA0), pyb.Pin(pyb.Pin.board.PA1), 5)
    
    
    # Instantiates three motor driver objects with appropriate pins and timer number
    pinB5 = pyb.Pin(pyb.Pin.board.PB5, pyb.Pin.OUT_PP)
    pinB3 = pyb.Pin(pyb.Pin.board.PB3, pyb.Pin.OUT_PP)
    
    motor1 = RoboMotorDriver.RoboMotorDriver(pinB5, pinB3, 2, 2)
    
    # Motor 2
    pinA6 = pyb.Pin(pyb.Pin.board.PA6, pyb.Pin.OUT_PP)
    pinA7 = pyb.Pin(pyb.Pin.board.PA7, pyb.Pin.OUT_PP)
    
    motor2 = RoboMotorDriver.RoboMotorDriver(pinA6, pinA7, 3, 2)
    
    # Motor 3
    pinA9 = pyb.Pin(pyb.Pin.board.PA9, pyb.Pin.OUT_PP)
    pinB4 = pyb.Pin(pyb.Pin.board.PB4, pyb.Pin.OUT_PP)
    
    motor3 = RoboMotorDriver.RoboMotorDriver(pinA9, pinB4, 3, 1)
    
    try:
        # Start motor 1, 2, 3
        motor1.set_duty_cycle(20)
        motor2.set_duty_cycle(20)
        motor3.set_duty_cycle(20)
        
        time = utime.ticks_ms()
        
        #while utime.ticks_ms() < (time + 10000):
        while True:
            encoder1.update()
            encoder2.update()
            encoder3.update()
            
            if (utime.ticks_ms() > (time + 50)):
                print("\ntimer counter1:", encoder1.timer.counter())
                print("\nencoder driver1", encoder1.read())
                
                print("\ntimer counter2:", encoder2.timer.counter())
                print("\nencoder driver2", encoder2.read())
                
                print("\ntimer counter3:", encoder3.timer.counter())
                print("\nencoder driver3", encoder3.read())
                
                if encoder1.read() > 360:
                    break
                time += 50
                
    except KeyboardInterrupt:
        motor1.set_duty_cycle(0)
        motor2.set_duty_cycle(0)
        motor3.set_duty_cycle(0)

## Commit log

2022-02-17 cad directory added
    CAD
    [01_Base_Plate.SLDPRT]
2022-02-17 Readme updates with BOM and Cad section
2022-02-17 couple readme changes
2022-02-17 add touch panel stuff from 305
    [01_Base_Plate.SLDPRT]
2022-02-18 updated BOM
2022-02-18 take out old motors
2022-02-18 CAD and readme update
    Pushed new CAD and readme
    [01_Base_Plate.SLDPRT, 02_A_Link.SLDPRT, 03_B_Link.SLDPRT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]
2022-02-24 some pic adds and cad changes
    Some stuff done here
    [10_Full_3R_Assembly.SLDASM]
2022-02-24 Updated CAD
    Rev 2 motor and solenoid added.
    Links changed to same length for a and b.
    Base plate hole spacing changed to equilateral triangle.
    Simulation not helping with range of motion estimates, playing with Solidworks is better.
    [01_Base_Plate.SLDPRT, 02_A_Link.SLDPRT, 03_B_Link.SLDPRT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]
2022-02-27 Changes as of yet
    Lots of changes here
    [01_Base_Plate.SLDPRT, 02_A_Link.SLDPRT, 03_B_Link.SLDPRT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]
2022-02-28 Changes (more)
    Lots of CAD
    [02_A_Link.SLDPRT, 03_B_Link.SLDPRT, 04_Platform.SLDPRT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]
2022-02-28 CAD Update
    Shaft Collars
    More shoulder bolts
    [07_Motor_rev2.SLDPRT, 10_Full_3R_Assembly_rev2.SLDASM, Motor_Mount.SLDPRT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]
2022-03-01 Updated CAD
    With set screw shaft collars, spacers
    [04_Platform.SLDPRT, 10_Full_3R_Assembly_rev2.SLDASM, 6056N14_Carbon Steel Set Screw Collar.SLDPRT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]
2022-03-02 Added Solenoid
    Solenoid and pen holder added
    [05_Pen.SLDPRT, 10_Full_3R_Assembly_rev2.SLDASM, PenHolder.SLDPRT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]
2022-03-02 Added nuts and bolts
    Added hardware for mounting pen mount and shoulder bolts
    [04_Platform.SLDPRT, 10_Full_3R_Assembly_rev2.SLDASM, PenHolder.SLDPRT]
2022-03-02 preliminary motor driver for new board
2022-03-03 pointless cad logs
2022-03-03 Added hardware
    More screws and nuts
    [10_Full_3R_Assembly_rev2.SLDASM, 90604A539_Pan Head Combination Phillips Slotted Screws.SLDPRT, 95462A029_Medium-Strength Steel Hex Nut.SLDPRT]
2022-03-03 update ball holder...temp files
    [09_Ball_Holder.SLDPRT]
2022-03-03 Able to spin 3 motors and read encoders
2022-03-06 limit switch cad
    [12_Limit_Mount.SLDPRT, 13_Limit_Ramp.SLDPRT]
2022-03-06 Joint task and closed loop updates
2022-03-06 Base plate update
    Holes in base plate, REV 4 UPDATE
    [01_Base_Plate.SLDPRT, 01_Base_Plate_rev2.SLDPRT, 01_Base_Plate_rev3.SLDPRT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]
2022-03-07 CAD Real Life Integration
    Updated parts with dimensions that match the real life geometry so that the workspace would be accurate
    [01_Base_Plate_rev4.SLDPRT, 02_A_Link.SLDPRT, 03_B_Link.SLDPRT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]
2022-03-09 badabing badaboom solenoid
2022-03-09 finalize 3d printed parts
    [PenHolder.SLDPRT, PenHoldingAssembly.SLDASM, SolenoidAssembly.SLDASM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]
2022-03-10 limit switch pic
2022-03-10 BIG BOI UPDATES
    works....with some little startup bugs
    [ClosedLoop.py, JointTask.py, RoboEncoderDriver.py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]
2022-03-10 Updated Code
    Demo day code
    [10_Full_3R_Assembly_rev4.SLDASM, Master_Link.DXF, Master_Link.SLDPRT]
2022-03-16 Fixed run method in tasktouch
    [TaskTouch.py]
2022-03-16 update BOM
2022-03-16 bom update
2022-03-21 Project Budget
    Spreadsheet added
    [ProjectBudget.xlsx]
